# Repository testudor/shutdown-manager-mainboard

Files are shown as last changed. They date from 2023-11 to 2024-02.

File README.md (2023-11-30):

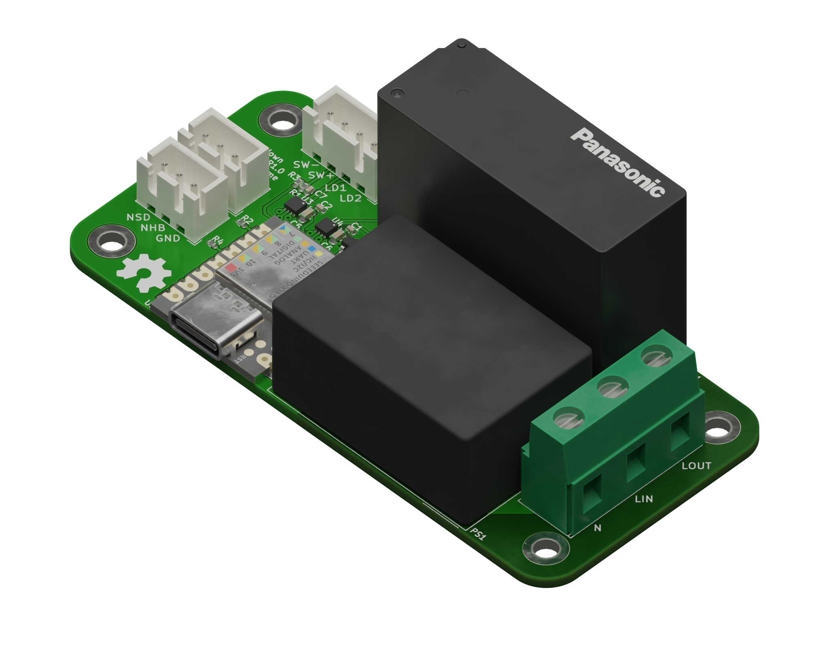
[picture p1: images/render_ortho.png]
render of the shutdown manager mainboard.


# Shutdown Manager Mainboard

This is a board for switching the AC mains input in machines such as 3D printers or CNC machines.

It is designed to be controlled by a push button switch with built-in dual color LEDs. An on-board LED driver controls these LEDs and different light patterns indicate the current system status.

The board has connections for two "nodes". These are external devices that require a safe shutdown procedure, such as a Raspberry Pi. It will trigger a shutdown of the nodes and will not turn off the power until they have completely shut down.

It is specifically designed to handle high inrush currents from SMPSs, which can cause normal relays to have their contacts weld together.

## I/O

### Nodes

| Pin | Function |
|-----|---|
| NSD | Node Shutdown - is repeatedly cycled low and high to trigger a shutdown of external devices  |
| NHB | Node Heart Beat - should be driven HIGH, when a node is running and LOW when it's shut down. |

For an easy way to connect a Raspberry Pi see [this repo.](https://github.com/testudor/shutdown-manager-rpi-node)

### Push button switch

| Pin | Function |
|---|---|
| SW-/SW+ | Connected to the power switch. |
| LD1/LD2 | Connected to the switches' dual color LED. |

I can recommend the ONPOW GQ19F-10E/RG/12/S, however any push button switch with 12V dual color LEDs should work. By dual color I mean LEDs which change their color based on polarity.

## Assembly

All necessary files can be found in the release section. They are compatible with the usual fab houses.

To use the full 16A this board was designed for, get 2oz PCBs or liberally coat the mains voltage traces on the bottom in solder.

I'm leaving these instructions intentionally vague as this is *NOT* a beginner's project. The more experienced should know what to do.

## Firmware

This board requires firmware to be flashed and configured. For details see [this repo.](https://github.com/testudor/shutdown-manager-firmware)

## Disclaimer

**WARNING:**

This board was designed to the best of my knowledge, but I am *NOT* an electrical engineer. If you decide to build this, I am not liable for damages or harm to yourself or anyone else.

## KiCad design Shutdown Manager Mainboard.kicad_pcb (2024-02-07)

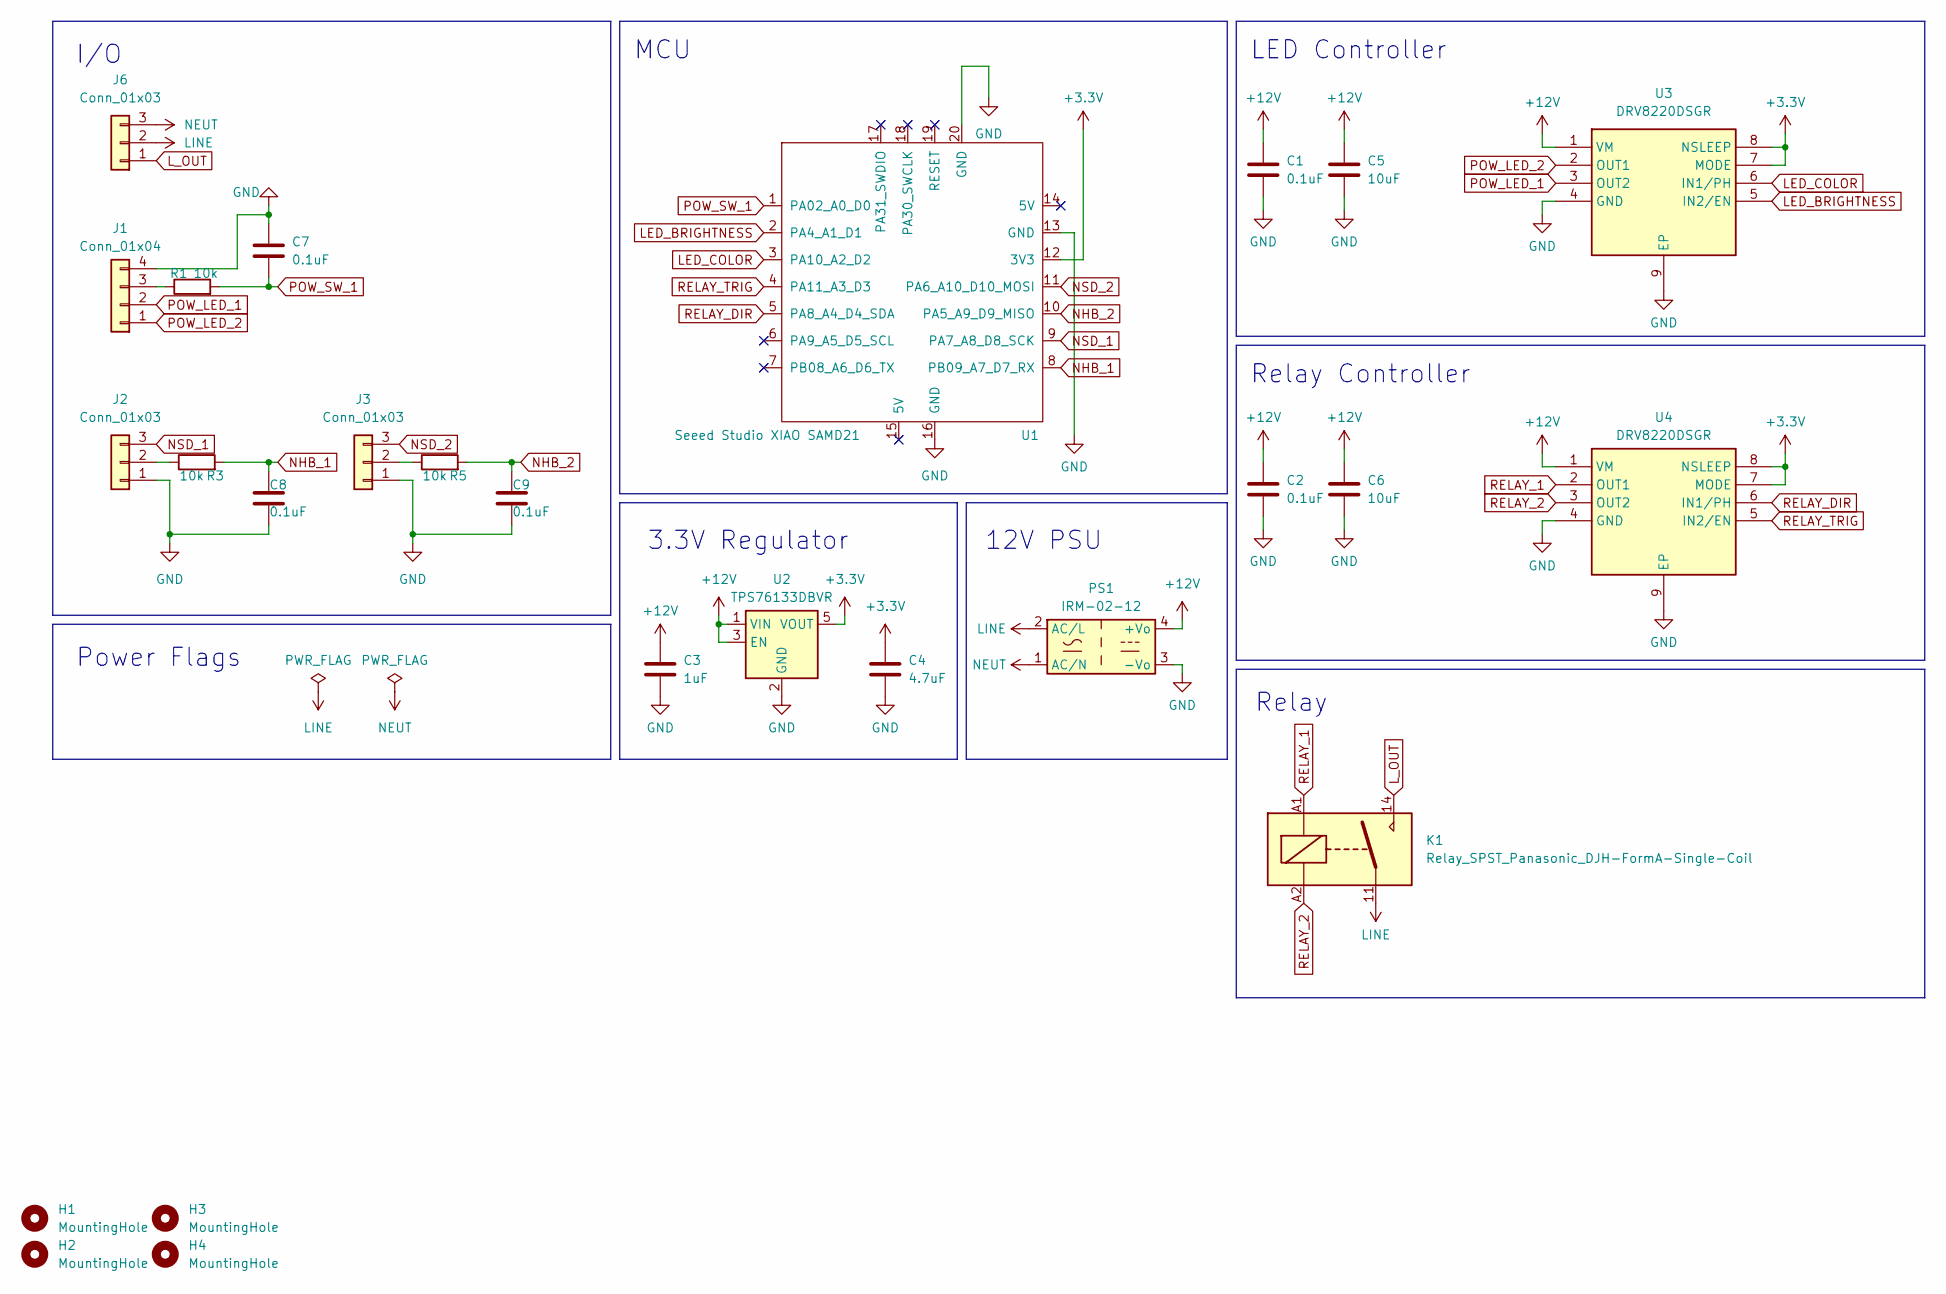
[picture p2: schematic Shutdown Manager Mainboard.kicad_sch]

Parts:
C1, C2, C7, C8, C9: 0.1uF; C_0402_1005Metric; MPN C1525
C3: 1uF; C_0402_1005Metric; MPN C52923
C4: 4.7uF; C_0603_1608Metric; MPN C19666
C5, C6: 10uF; C_0603_1608Metric; MPN C96446
H1, H2, H3, H4: MountingHole; MountingHole_3.2mm_M3_ISO7380_Pad_TopBottom
J1: Conn_01x04; JST_XH_B4B-XH-A_1x04_P2.50mm_Vertical; MPN C722867
J2, J3: Conn_01x03; JST_XH_B3B-XH-A_1x03_P2.50mm_Vertical; MPN C722863
J6: Conn_01x03; 282844-3; MPN C591951
K1: Relay_SPST_Panasonic_DJH-FormA-Single-Coil
PS1: IRM-02-12; Converter_ACDC_MeanWell_IRM-02-xx_THT
R1, R3, R5: 10k; R_0402_1005Metric; MPN C25744
U1: Seeed Studio XIAO SAMD21; XIAO-SAMD21-RP2040-14P-2.54-21X17.8MM (Seeeduino XIAO)
U2: TPS76133DBVR; SOT-23-5; MPN C194885
U3, U4: DRV8220DSGR; WSON-8-1EP_2x2mm_P0.5mm_EP0.9x1.6mm; Manufacturer_Part_Number DRV8220DSGR; Mouser Part Number 595-DRV8220DSGR

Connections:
+3.3V: C4.1, U1.12 (3V3), U2.5 (VOUT), U3.7 (MODE), U3.8 (NSLEEP), U4.7 (MODE), U4.8 (NSLEEP)
+12V: C1.1, C2.1, C3.1, C5.1, C6.1, PS1.4 (+Vo), U2.1 (VIN), U2.3 (EN), U3.1 (VM), U4.1 (VM)
GND: C1.2, C2.2, C3.2, C4.2, C5.2, C6.2, C7.1, C8.2, C9.2, J1.4, J2.1, J3.1, PS1.3 (-Vo), U1.13 (GND), U1.16 (GND), U1.20 (GND), U2.2 (GND), U3.4 (GND), U3.9 (EP), U4.4 (GND), U4.9 (EP)
LED_BRIGHTNESS: U1.2 (PA4_A1_D1), U3.5 (IN2/EN)
LED_COLOR: U1.3 (PA10_A2_D2), U3.6 (IN1/PH)
LINE: J6.2, K1.11, PS1.2 (AC/L)
L_OUT: J6.1, K1.14
NEUT: J6.3, PS1.1 (AC/N)
NHB_1: C8.1, R3.2, U1.8 (PB09_A7_D7_RX)
NHB_2: C9.1, R5.2, U1.10 (PA5_A9_D9_MISO)
NSD_1: J2.3, U1.9 (PA7_A8_D8_SCK)
NSD_2: J3.3, U1.11 (PA6_A10_D10_MOSI)
unnamed: J1.3, R1.1
unnamed: J2.2, R3.1
unnamed: J3.2, R5.1
POW_LED_1: J1.2, U3.3 (OUT2)
POW_LED_2: J1.1, U3.2 (OUT1)
POW_SW_1: C7.2, R1.2, U1.1 (PA02_A0_D0)
RELAY_1: K1.A1, U4.2 (OUT1)
RELAY_2: K1.A2, U4.3 (OUT2)
RELAY_DIR: U1.5 (PA8_A4_D4_SDA), U4.6 (IN1/PH)
RELAY_TRIG: U1.4 (PA11_A3_D3), U4.5 (IN2/EN)

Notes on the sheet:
Relay
MCU
12V PSU
3.3V Regulator
LED Controller
Relay Controller
Power Flags
I/O

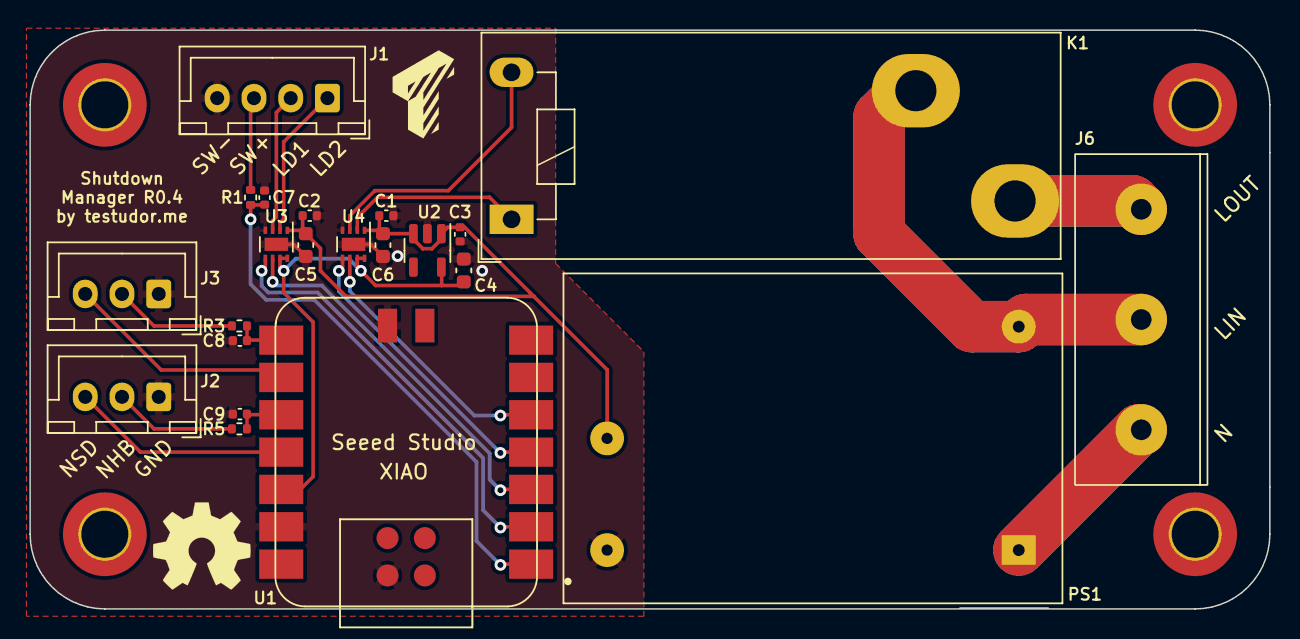
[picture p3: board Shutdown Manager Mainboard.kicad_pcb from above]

Board: 2 copper layers, 84.3 x 39.4 mm, 26 parts (0 on the bottom side), 22 nets.

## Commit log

2023-11-29 Added strong external pullup/-down resistors to inputs, Added RC filter to main power button input
    [Shutdown Manager Mainboard.kicad_pcb, Shutdown Manager Mainboard.kicad_sch]
2024-02-07 Fixed heartbeat input filtering
    [Shutdown Manager Mainboard.kicad_pcb, Shutdown Manager Mainboard.kicad_sch]
